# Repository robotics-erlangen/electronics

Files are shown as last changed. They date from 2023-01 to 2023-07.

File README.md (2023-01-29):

# Robotics Erlangen e.V. &ndash; Open Source SSL Robot Hardware
Raw and compiled files for the open source hardware of the German SSL team ER-Force.

## Commit Structure
Commits that have been tagged represent a self-contained robot state,
i.e. the PCB's and mechanical components work well with each other.

## Folder Structure
At the top level of the repository, there is a separate folder for each robot generation.
Currently, only parts of our latest robot generation 'pasta' have been published.
Each robot generation is divided into two sections: mechanics and electronics.

The electronics section has the following structure:
- boards: Contains a separate folder for each PCB that is part of the robot
- eagle: Contains generic libraries, design rule files, etc.

Within each PCB's folder, there are multiple subfolders:
- documents: A pdf version of the schematics as well as optional documentation
- eagle: The schematics and layout in the raw EAGLE file format, i.e.
  - the schematics (*.sch)
  - the layout (*.brd)
  - a library with all board-specific, non-generic components (*.lbr)
  - the design rule file used (*.dru)
  - the cam job used to generate the gerber files (*.cam)
- gerber: The compiled layout files, i.e.
  - the Gerber files
  - the Excellon drill files
  - the Pick & Place files for the top and bottom side
  - a bill of materials

## Example
- ```/pasta```: all files related to the 'pasta' generation
- ```/pasta/electronics```: electronic files for the 'pasta' generation
- ```/pasta/electronics/eagle```: generic eagle files usable accross multiple 'pasta' PCBs
- ```/pasta/electronics/boards```: all PCBs used in the 'pasta' generation
- ```/pasta/electronics/boards/kicker```: all data related to the kicker board of the 'pasta' generation
- ```/pasta/electronics/boards/kicker/eagle```: the raw eagle data of the kicker board
- ```/pasta/electronics/boards/kicker/gerber```: the compiled files of the kicker board
- ```/pasta/electronics/boards/kicker/documents```: additional documentation for the kicker board (e.g. schematics as pdf)

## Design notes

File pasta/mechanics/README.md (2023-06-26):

### What is this repository for? ###

* CAD data for the mechanics of Robotics-Erlangen e.V.
* Generation 2023
* Created  in Autodesk Inventor 2023

### How do I get set up? ###

Project file: When starting Inventor, always make sure that 'OpenSource_2023.ipj' is selected as the active project file. The path in which the working directory is located is noted there for Inventor.

### Folder structure ###

In the file 'Robot_2023.iam' is the assembly of the entire robot. Each folder is assigned to a module of the robot. The production drawings of the components of the modules are stored in the respective folders under 'drawings'. Furthermore, there is the folder 'STEP', where a step file of the robot's assembly can be found, and the folder 'Object_Data', where an object file of the robot is stored. Content centre files are stored in the folder 'ContenCenter-Files'. This concerns all standard parts that are installed via the Content Centre. Other imported parts are stored in the respective subfolders for the corresponding assemblies. The file 'purchased_parts.xlsx' contains a list of our purchased parts.

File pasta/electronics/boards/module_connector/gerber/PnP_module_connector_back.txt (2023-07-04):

C101	-24.50	31.50	90.00	100n ±10% 50V X7R	C0603
C102	-24.50	0.50	90.00	100n ±10% 50V X7R	C0603
C103	24.50	30.50	270.00	100n ±10% 50V X7R	C0603
C104	-24.50	-30.50	90.00	100n ±10% 50V X7R	C0603
C105	24.50	-31.50	270.00	100n ±10% 50V X7R	C0603
C106	24.50	-0.50	270.00	100n ±10% 50V X7R	C0603
C107	5.00	-10.00	90.00	100n ±10% 50V X7R	C0603
J101	0.00	10.00	180.00		610016243021
J102	-35.00	31.00	90.00		610016243021
J103	-35.00	0.00	90.00		610016243021
J104	-35.00	-31.00	90.00		610016243021
J105	35.00	-31.00	270.00		610016243021
J106	35.00	0.00	270.00		610016243021
J107	35.00	31.00	270.00		610016243021
J201	60.00	42.73	270.00		610004243021
J202	60.00	19.27	90.00		610004243021
J203	60.00	11.73	270.00		610004243021
J204	60.00	-11.73	90.00		610004243021
J205	60.00	-19.27	270.00		610004243021
J206	60.00	-42.73	90.00		610004243021
J207	-60.00	-42.73	90.00		610004243021
J208	-60.00	-19.27	270.00		610004243021
J209	-60.00	-11.73	90.00		610004243021
J210	-60.00	11.73	270.00		610004243021
J211	-60.00	19.27	90.00		610004243021
J212	-60.00	42.73	270.00		610004243021
J213	-11.73	35.00	180.00		610004243021
J214	11.73	35.00	0.00		610004243021
R101	1.50	-13.00	180.00	3k3 ±1% 75V 0.1W	R0603
R102	-28.00	28.50	180.00	3k3 ±1% 75V 0.1W	R0603
R103	-28.00	-2.50	180.00	3k3 ±1% 75V 0.1W	R0603
R104	-28.00	-33.50	180.00	3k3 ±1% 75V 0.1W	R0603
R105	28.00	-28.50	0.00	3k3 ±1% 75V 0.1W	R0603
R106	28.00	2.50	0.00	3k3 ±1% 75V 0.1W	R0603
R107	28.00	33.50	0.00	3k3 ±1% 75V 0.1W	R0603
SHORT101	-12.00	1.25	180.00	SHORT0.254	SHORT0.254
SHORT102	-5.00	48.00	0.00	SHORT0.254	SHORT0.254
SHORT105	0.00	-47.00	180.00	SHORT0.254	SHORT0.254
SHORT108	15.00	48.00	0.00	SHORT0.254	SHORT0.254
U101	1.50	-10.00	180.00	SN74AUP1G126DBVR	SOT23-5
U102	-28.00	31.50	180.00	SN74AUP1G126DBVR	SOT23-5
U103	-28.00	0.50	180.00	SN74AUP1G126DBVR	SOT23-5
U104	-28.00	-30.50	180.00	SN74AUP1G126DBVR	SOT23-5
U105	28.00	-31.50	0.00	SN74AUP1G126DBVR	SOT23-5
U106	28.00	-0.50	0.00	SN74AUP1G126DBVR	SOT23-5
U107	28.00	30.50	0.00	SN74AUP1G126DBVR	SOT23-5

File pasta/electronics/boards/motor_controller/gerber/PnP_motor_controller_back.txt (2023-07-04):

C101	14.50	16.00	0.00	100n ±10% 50V X5R	C0402
C102	9.50	33.50	180.00	1u ±10% 25V X5R	C0402
C103	3.50	4.00	180.00	4u7 ±20% 6V3 X5R	C0603
C104	3.50	6.00	180.00	4u7 ±20% 6V3 X5R	C0603
C201	15.00	12.00	180.00	100n ±10% 50V X5R	C0402
C203	8.00	12.50	270.00	4u7 ±20% 6V3 X5R	C0603
C204	6.00	13.50	270.00	100n ±10% 50V X5R	C0402
C205	10.50	12.00	90.00	100n ±10% 50V X5R	C0402
C206	9.50	15.50	270.00	100n ±10% 50V X5R	C0402
C207	10.50	15.50	270.00	1u ±10% 25V X5R	C0402
C208	11.50	13.00	270.00	100n ±10% 50V X5R	C0402
D401	-8.50	23.00	270.00	D15V0M1U2LP3	D15V0M1U2LP3
D402	-10.50	23.00	270.00	D15V0M1U2LP3	D15V0M1U2LP3
D403	-2.50	21.00	0.00	D15V0M1U2LP3	D15V0M1U2LP3
D404	0.50	21.00	0.00	D15V0M1U2LP3	D15V0M1U2LP3
D405	11.50	22.50	270.00	D15V0M1U2LP3	D15V0M1U2LP3
D406	9.50	24.00	180.00	D15V0M1U2LP3	D15V0M1U2LP3
L101	0.50	5.00	90.00	742792692	WE-CBF_0603(W=2.6)
R102	14.50	18.00	0.00	1k ±1% 50V 62.5mW	R0402
R201	6.00	7.50	0.00	1k ±1% 50V 62.5mW	R0402
R203	-3.00	34.50	270.00	1k ±1% 50V 62.5mW	R0402
R204	-5.00	34.50	270.00	1k ±1% 50V 62.5mW	R0402
R205	3.00	34.50	270.00	1k ±1% 50V 62.5mW	R0402
R302	5.50	10.00	270.00	1k ±1% 50V 62.5mW	R0402
R403	-12.50	23.00	270.00	0R ±1% 50V 62.5mW	R0402
R404	0.50	23.00	0.00	0R ±1% 50V 62.5mW	R0402
R407	-7.50	24.00	90.00	0R ±1% 50V 62.5mW	R0402
R408	-2.50	23.00	0.00	0R ±1% 50V 62.5mW	R0402
R409	-9.50	23.00	90.00	n.c.   	R0402
R410	-11.50	23.00	90.00	n.c.   	R0402
R411	-2.50	22.00	180.00	n.c.   	R0402
R412	0.50	22.00	180.00	n.c.   	R0402
R414	8.00	25.50	270.00	0R ±1% 50V 62.5mW	R0402
R416	9.50	22.50	270.00	0R ±1% 50V 62.5mW	R0402
R417	10.50	22.50	90.00	n.c.   	R0402
R418	9.50	25.00	0.00	n.c.   	R0402
Z103	-5.00	25.50	180.00	ESD8704	UDFN10
Z104	-2.00	25.50	180.00	ESD8704	UDFN10
Z105	5.00	25.50	180.00	ESD7004	UDFN10

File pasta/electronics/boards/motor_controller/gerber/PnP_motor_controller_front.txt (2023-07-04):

C105	-5.00	4.50	270.00	100n ±10% 50V X5R	C0402
C106	-4.00	4.50	270.00	1u ±10% 25V X5R	C0402
C107	-1.50	4.50	270.00	100n ±10% 50V X5R	C0402
C108	-0.50	4.50	270.00	1u ±10% 25V X5R	C0402
C202	12.50	8.50	270.00	100n ±10% 50V X5R	C0402
C301	-6.80	7.00	180.00	100n ±10% 50V X5R	C0402
C302	-12.50	15.50	270.00	100u ±20% 35V	865080545012
C303	-6.00	14.00	90.00	10u ±20% 50V X5R	C1206
C304	-3.50	14.50	90.00	100n ±10% 50V X7R	C0603
C305	-3.50	12.00	0.00	1u ±10% 25V X5R	C0402
C306	-0.25	16.00	90.00	1u ±10% 25V X5R	C0402
C307	-2.00	16.00	90.00	47n ±10% 50V X5R	C0402
C308	0.75	16.00	90.00	1u ±10% 25V X5R	C0402
C401	-13.00	24.50	90.00	n.c.   	C0402
C402	3.00	23.50	90.00	n.c.   	C0402
C403	-10.00	20.50	0.00	1u ±10% 50V X5R	C0603
C404	-1.00	19.50	180.00	1u ±10% 50V X5R	C0603
C405	-6.50	24.50	270.00	n.c.   	C0402
C406	-4.50	23.50	270.00	n.c.   	C0402
C407	7.00	23.50	90.00	n.c.   	C0402
C408	10.00	19.50	0.00	1u ±10% 50V X5R	C0603
C409	13.00	23.50	270.00	n.c.   	C0402
D201	0.00	35.00	180.00	150066M153000	WL-SFCX_0606
F101	-13.00	5.00	180.00	5A	157T
L102	-1.50	6.50	0.00	782632102	WE-CBF_0603(W=2.6)
R101	-5.00	6.50	90.00	2R2 ±1% 50V 62.5mW	R0402
R202	9.50	8.50	90.00	1k ±1% 50V 62.5mW	R0402
R301	-14.34	9.50	270.00	FC4L32R010FER	FC4L32
R401	-12.00	26.50	180.00	n.c.   	R0603
R402	2.00	25.50	0.00	n.c.   	R0603
R405	-8.00	26.50	180.00	n.c.   	R0603
R406	-2.00	25.50	0.00	n.c.   	R0603
R413	8.00	25.50	180.00	n.c.   	R0603
R415	12.00	25.50	180.00	n.c.   	R0603
SHORT101	-7.50	15.50	0.00	SHORT4.35	SHORT4.35
SHORT102	-5.95	6.00	180.00	SHORT2.4	SHORT2.4
SHORT103	-5.95	4.00	180.00	SHORT2.4	SHORT2.4
SHORT301	-4.50	12.00	0.00	SHORT2.4	SHORT2.4
T401	-10.00	23.50	0.00	SIZ260DT	SIZ260DT
T402	0.00	22.50	180.00	SIZ260DT	SIZ260DT
T403	10.00	22.50	0.00	SIZ260DT	SIZ260DT
U101	14.50	17.00	270.00	SN74AHC1G125DBVR	SOT23-5
U201	8.50	13.50	180.00	STM32F373V8H6	STM32F373V8H6
U202	11.00	8.50	270.00	24CW1280T-I/CS0668	CS0-4
U301	-9.00	9.50	0.00	INA240A3PWR	TSSOP-8
U302	1.00	12.00	0.00	DRV8350FSRTVR	QFN50P500X500X80-33T345
Y201	14.50	12.00	90.00	8 MHz	830207192009
Z101	5.50	5.00	0.00	ESD8704	UDFN10
Z102	8.50	5.00	0.00	ESD8704	UDFN10

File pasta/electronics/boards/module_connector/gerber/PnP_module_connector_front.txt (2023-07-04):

C108	14.00	-48.00	270.00	10u ±20% 50V X5R	C1206
C109	23.50	-6.50	270.00	10u ±20% 50V X5R	C1206
C110	-23.50	5.50	270.00	10u ±20% 50V X5R	C1206
J108	1.27	-73.00	270.00		610004243021
J109	0.00	-50.00	180.00	610016243021	610X16243021
SHORT103	-45.00	15.50	270.00	SHORT0.254	SHORT0.254
SHORT104	-45.00	-15.50	270.00	SHORT0.254	SHORT0.254
SHORT106	45.00	-15.50	90.00	SHORT0.254	SHORT0.254
SHORT107	45.00	15.50	90.00	SHORT0.254	SHORT0.254
TP201	80.00	24.00	270.00	TESTPAD	TESTPAD
TP202	80.00	20.00	270.00	TESTPAD	TESTPAD
TP203	80.00	12.00	270.00	TESTPAD	TESTPAD
TP204	80.00	16.00	270.00	TESTPAD	TESTPAD
TP205	80.00	6.00	0.00	TESTPAD	TESTPAD
TP206	80.00	2.00	0.00	TESTPAD	TESTPAD
TP207	80.00	-2.00	0.00	TESTPAD	TESTPAD
TP208	80.00	-6.00	0.00	TESTPAD	TESTPAD
TP209	80.00	-16.00	0.00	TESTPAD	TESTPAD
TP210	80.00	-12.00	0.00	TESTPAD	TESTPAD
TP211	80.00	-20.00	0.00	TESTPAD	TESTPAD
TP212	80.00	-24.00	0.00	TESTPAD	TESTPAD
TP213	-80.00	-24.00	0.00	TESTPAD	TESTPAD
TP214	-80.00	-20.00	0.00	TESTPAD	TESTPAD
TP215	-80.00	-12.00	0.00	TESTPAD	TESTPAD
TP216	-80.00	-16.00	0.00	TESTPAD	TESTPAD
TP217	-80.00	-6.00	0.00	TESTPAD	TESTPAD
TP218	-80.00	-2.00	0.00	TESTPAD	TESTPAD
TP219	-80.00	2.00	0.00	TESTPAD	TESTPAD
TP220	-80.00	6.00	0.00	TESTPAD	TESTPAD
TP221	-80.00	16.00	0.00	TESTPAD	TESTPAD
TP222	-80.00	12.00	0.00	TESTPAD	TESTPAD
TP223	-80.00	20.00	0.00	TESTPAD	TESTPAD
TP224	-80.00	24.00	0.00	TESTPAD	TESTPAD
TP225	-23.50	43.00	0.00	TESTPAD	TESTPAD
TP226	-23.50	47.00	180.00	TESTPAD	TESTPAD
TP227	23.50	47.00	0.00	TESTPAD	TESTPAD
TP228	23.50	43.00	180.00	TESTPAD	TESTPAD

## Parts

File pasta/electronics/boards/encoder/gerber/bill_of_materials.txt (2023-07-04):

Stückliste exportiert aus D:/hardware/pasta/electronics/boards/encoder/eagle/encoder.sch am 04.07.2023 16:03

Part Value        Device                Package      Description                                                                                      CAPACITANCE COPYRIGHT                                                DIELECTRIC MF                        MOUSER               MPN               POWER RESISTANCE TOLERANCE VOLTAGE
C101 4u7 6V3      C(4.7UF,50V,0805)     C0805        Robotics Erlangen Capacitor Library                                                              4u7                                                                  X5R        Samsung                                        CL21A475KBQNNNE                    ±10%      50V    
C102 100n 6V3     C(100NF,50V,0603)     C0603        Robotics Erlangen Capacitor Library                                                              100n                                                                 X7R        Würth Elektronik                               885012206095                       ±10%      50V    
C103 10u 6V3      C(10UF,6.3V,0603)     C0603        Robotics Erlangen Capacitor Library                                                              10u                                                                  X5R        Würth Elektronik                               885012106006                       ±20%      6V3    
C104 10n 50V      C(10NF,50V,0603)      C0603        Robotics Erlangen Capacitor Library                                                              10n                                                                  X7R        Würth Elektronik                               885012206089                       ±10%      50V    
C105 100n 6V3     C(100NF,50V,0603)     C0603        Robotics Erlangen Capacitor Library                                                              100n                                                                 X7R        Würth Elektronik                               885012206095                       ±10%      50V    
D101 PTVS3V3S1UR  PTVS3V3S1UR           SOD123                                                                                                                                                                                        Nexperia                  771-PTVS3V3S1UR115    PTVS3V3S1UR,115                                    
J101 690367281076 690367281076          690367281076 WR-MM Female SMT Connector with Polarization, 10 Pins=>Code : Con_BTB_MM_Female_SMT_690367281076                                                                                 Würth Elektronik                               690367281076                                        
R101 10k          R(10K,75V,0.1W,0603)  R0603        Robotics Erlangen Resistor Library                                                                                                                                               YAGEO                                          RC0603FR-0710KL   0.1W  10k        ±1%       75V    
R102 10k          R(10K,75V,0.1W,0603)  R0603        Robotics Erlangen Resistor Library                                                                                                                                               YAGEO                                          RC0603FR-0710KL   0.1W  10k        ±1%       75V    
R103 100R         R(100R,75V,0.1W,0603) R0603        Robotics Erlangen Resistor Library                                                                                                                                               YAGEO                                          RC0603FR-07100RL  0.1W  100R       ±1%       75V    
R104 100R         R(100R,75V,0.1W,0603) R0603        Robotics Erlangen Resistor Library                                                                                                                                               YAGEO                                          RC0603FR-07100RL  0.1W  100R       ±1%       75V    
R105 100R         R(100R,75V,0.1W,0603) R0603        Robotics Erlangen Resistor Library                                                                                                                                               YAGEO                                          RC0603FR-07100RL  0.1W  100R       ±1%       75V    
R106 100R         R(100R,75V,0.1W,0603) R0603        Robotics Erlangen Resistor Library                                                                                                                                               YAGEO                                          RC0603FR-07100RL  0.1W  100R       ±1%       75V    
R107 1k           R(1.0K,75V,0.1W,0603) R0603        Robotics Erlangen Resistor Library                                                                                                                                               YAGEO                                          RC0603FR-071KL    0.1W  1k         ±1%       75V    
R108 1k           R(1.0K,75V,0.1W,0603) R0603        Robotics Erlangen Resistor Library                                                                                                                                               YAGEO                                          RC0603FR-071KL    0.1W  1k         ±1%       75V    
T101 BSS123       BSS123                SOT23-3      N-CHANNEL MOS FET                                                                                                                                                                Nexperia                  726-BSS123NH6327XTSA BSS123NH6327XTSA1                                   
U101 AS5048A-HTSP AS5048A-HTSP          AS5048A-HTSP                                                                                                                                                                                  ams                       985-AS5048A-HTSP-500 AS5048A-HTSP                                        
U102 MAX9130EXT+T MAX9130EXT+T          21-0077G_MXM                                                                                                              Copyright (C) 2021 Ultra Librarian. All rights reserved.            Maxim Integrated Products                      MAX9130EXT+T                                        
U103 SN65LVDS050D SN65LVDS050D          SOIC-16                                                                                                                                                                                       Texas Instruments                              SN65LVDS050D

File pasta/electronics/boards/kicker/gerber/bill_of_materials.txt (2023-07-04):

Stückliste exportiert aus D:/hardware/pasta/electronics/boards/kicker/eagle/kicker.sch am 04.07.2023 12:32

Part  Value                  Device                         Package                Description                                                                                                          CAPACITANCE DIELECTRIC LINE1     LINE2      MF                           MOUSER               MPN                 POWER RESISTANCE TOLERANCE VALUE               VOLTAGE
C101  270  µF                WCAP-PSLC_10X12.4_875075661009 WCAP-PSLC_10X12.4(DXL) WCAP-PSLC Aluminum Polymer Capacitors                                                                                                                            Würth Elektronik                                  875075661009                         ±10%      270  µF             35V(DC)
C102  10u ±20% 50V X5R       C(10UF,50V,1206)               C1206                  Robotics Erlangen Capacitor Library                                                                                  10u         X5R        10u ±20%  50V X5R    Samsung                                           CL31A106MBHNNNE                      ±20%      10u ±20% 50V X5R    50V    
C103  100n ±10% 50V X7R      C(100NF,50V,0603)              C0603                  Robotics Erlangen Capacitor Library                                                                                  100n        X7R        100n ±10% 50V X7R    Würth Elektronik                                  885012206095                         ±10%      100n ±10% 50V X7R   50V    
C104  100n ±10% 50V X7R      C(100NF,50V,0603)              C0603                  Robotics Erlangen Capacitor Library                                                                                  100n        X7R        100n ±10% 50V X7R    Würth Elektronik                                  885012206095                         ±10%      100n ±10% 50V X7R   50V    
C105  4u7 ±10% 50V X5R       C(4.7UF,50V,0805)              C0805                  Robotics Erlangen Capacitor Library                                                                                  4u7         X5R        4u7 ±10%  50V X5R    Samsung                                           CL21A475KBQNNNE                      ±10%      4u7 ±10% 50V X5R    50V    
C106  100p ±5% 50V NP0       C(100PF,50V,0603)              C0603                  Robotics Erlangen Capacitor Library                                                                                  100p        NP0        100p ±5%  50V NP0    Würth Elektronik                                  885012006057                         ±5%       100p ±5% 50V NP0    50V    
C107  2n2 ±10% 50V X7R       C(2.2NF,50V,0603)              C0603                  Robotics Erlangen Capacitor Library                                                                                  2n2         X7R        2n2 ±10%  50V X7R    Würth Elektronik                                  885012206085                         ±10%      2n2 ±10% 50V X7R    50V    
C108  33n ±10% 50V X7R       C(33NF,50V,0603)               C0603                  Robotics Erlangen Capacitor Library                                                                                  33n         X7R        33n ±10%  50V X7R    Würth Elektronik                                  885012206092                         ±10%      33n ±10% 50V X7R    50V    
C109                         C(1210)                        C1210                  Robotics Erlangen Capacitor Library                                                                                  220nF       X7R        220n ±5%  100V X7R   KEMET                                             C0805C224J1RECTU                     ±5%                           100V   
C110  n.c.                   C(N.C.,1206)                   C1206                  Robotics Erlangen Capacitor Library                                                                                  n.c.                   n.c.                                                                                                                  n.c.                       
C111  n.c.                   C(N.C.,1206)                   C1206                  Robotics Erlangen Capacitor Library                                                                                  n.c.                   n.c.                                                                                                                  n.c.                       
C112  1000u 250V             ESMQ251VSN102MQ45S             ESMQ251VSN102MQ45S                                                                                                                                                                      United Chemi-Con             661-ESMQ251VSN102MQ4 ESMQ251VSN102MQ45S                                                        
C113  1000u 250V             ESMQ251VSN102MQ45S             ESMQ251VSN102MQ45S                                                                                                                                                                      United Chemi-Con             661-ESMQ251VSN102MQ4 ESMQ251VSN102MQ45S                                                        
C201  47n ±10% 50V X7R       C(47NF,50V,0603)               C0603                  Robotics Erlangen Capacitor Library                                                                                  47n         X7R        47n ±10%  50V X7R    Würth Elektronik                                  885012206093                         ±10%      47n ±10% 50V X7R    50V    
C202  47n ±10% 50V X7R       C(47NF,50V,0603)               C0603                  Robotics Erlangen Capacitor Library                                                                                  47n         X7R        47n ±10%  50V X7R    Würth Elektronik                                  885012206093                         ±10%      47n ±10% 50V X7R    50V    
C203  1u ±10% 50V X5R        C(1.0UF,50V,0603)              C0603                  Robotics Erlangen Capacitor Library                                                                                  1u          X5R        1u ±10%   50V X5R    Samsung                                           CL10A105KB8NNNC                      ±10%      1u ±10% 50V X5R     50V    
C204  1u ±10% 50V X5R        C(1.0UF,50V,0603)              C0603                  Robotics Erlangen Capacitor Library                                                                                  1u          X5R        1u ±10%   50V X5R    Samsung                                           CL10A105KB8NNNC                      ±10%      1u ±10% 50V X5R     50V    
C205  10u ±20% 50V X5R       C(10UF,50V,1206)               C1206                  Robotics Erlangen Capacitor Library                                                                                  10u         X5R        10u ±20%  50V X5R    Samsung                                           CL31A106MBHNNNE                      ±20%      10u ±20% 50V X5R    50V    
C206                         C(1210)                        C1210                  Robotics Erlangen Capacitor Library                                                                                  330n        X7T        330n ±10% X7T 250V   TDK                                               C3225X7T2E334K200AA                  ±10%                          250V   
C207  10u ±20% 50V X5R       C(10UF,50V,1206)               C1206                  Robotics Erlangen Capacitor Library                                                                                  10u         X5R        10u ±20%  50V X5R    Samsung                                           CL31A106MBHNNNE                      ±20%      10u ±20% 50V X5R    50V    
C208  10u ±20% 50V X5R       C(10UF,50V,1206)               C1206                  Robotics Erlangen Capacitor Library                                                                                  10u         X5R        10u ±20%  50V X5R    Samsung                                           CL31A106MBHNNNE                      ±20%      10u ±20% 50V X5R    50V    
C301  100n ±10% 50V X7R      C(100NF,50V,0603)              C0603                  Robotics Erlangen Capacitor Library                                                                                  100n        X7R        100n ±10% 50V X7R    Würth Elektronik                                  885012206095                         ±10%      100n ±10% 50V X7R   50V    
C302  100n ±10% 50V X7R      C(100NF,50V,0603)              C0603                  Robotics Erlangen Capacitor Library                                                                                  100n        X7R        100n ±10% 50V X7R    Würth Elektronik                                  885012206095                         ±10%      100n ±10% 50V X7R   50V    
C303  100n ±10% 50V X7R      C(100NF,50V,0603)              C0603                  Robotics Erlangen Capacitor Library                                                                                  100n        X7R        100n ±10% 50V X7R    Würth Elektronik                                  885012206095                         ±10%      100n ±10% 50V X7R   50V    
C304  2u2 ±10% 50V X7R       C(2.2UF,50V,0805)              C0805                  Robotics Erlangen Capacitor Library                                                                                  2u2         X7R        2u2 ±10%  50V X7R    Samsung                                           CL21B225KBYNNWE                      ±10%      2u2 ±10% 50V X7R    50V    
C305  100n ±10% 50V X7R      C(100NF,50V,0603)              C0603                  Robotics Erlangen Capacitor Library                                                                                  100n        X7R        100n ±10% 50V X7R    Würth Elektronik                                  885012206095                         ±10%      100n ±10% 50V X7R   50V    
D101                         LED5MM                         LED5MM                                                                                                                                                                                  Würth Elektronik                                  151054RS03000                                                             
D102  1N4148                 1N4148W                        SOD-123                DIODE                                                                                                                                                            Micro Commercial Components                       1N4148W                                                                   
D103  STTH212U               STTH212U                       SMB                    DIODE                                                                                                                                                            STMicroelectronics                                STTH212U                                                                  
D201  GB01SLT12-214          GB01SLT12-214                  DO-214                                                                                                                                                                                  GeneSiC                      905-GB01SLT06-214    GB01SLT06-214                                                             
D202  GB01SLT12-214          GB01SLT12-214                  DO-214                                                                                                                                                                                  GeneSiC                      905-GB01SLT06-214    GB01SLT06-214                                                             
D203  GB01SLT12-214          GB01SLT12-214                  DO-214                                                                                                                                                                                  GeneSiC                      905-GB01SLT06-214    GB01SLT06-214                                                             
D204  GB01SLT12-214          GB01SLT12-214                  DO-214                                                                                                                                                                                  GeneSiC                      905-GB01SLT06-214    GB01SLT06-214                                                             
H101                         9774060360R                    9774***360                                                                                                                                                                              Würth Elektronik                                  9774060360R                                                               
H102                         9774060360R                    9774***360                                                                                                                                                                              Würth Elektronik                                  9774060360R                                                               
H103                         9774060360R                    9774***360                                                                                                                                                                              Würth Elektronik                                  9774060360R                                                               
J301                         690367181672                   690367181672           WR-MM Female Connector without Latch and without Polarization, 16 Pins=>Code : Con_BTB_MM_Female_THT_St_690367181672                                             Würth Elektronik                                  690367181672                                                              
J302                         66100311622                    66100311622*           Male Vertical Shrouded Header                                                                                                                                    Würth Elektronik                                  66100311622                                                               
J303                         66100311622                    66100311622*           Male Vertical Shrouded Header                                                                                                                                    Würth Elektronik                                  66100311622                                                               
OP101 LTV-352T               LTV-352T                       DIL4-SMD               OPTO COUPLER                                                                                                                                                     Lite-On                      859-LTV-352T         LTV-352T                                                                  
OP201 LTV-352T               LTV-352T                       DIL4-SMD               OPTO COUPLER                                                                                                                                                     Lite-On                      859-LTV-352T         LTV-352T                                                                  
OP202 LTV-352T               LTV-352T                       DIL4-SMD               OPTO COUPLER                                                                                                                                                     Lite-On                      859-LTV-352T         LTV-352T                                                                  
Q101  FJT44TF                TRANSISTOR_NPN"                SOT223                 Transistor NPN                                                                                                                                                   onsemi / Fairchild                                FJT44TF                                                                   
Q102  TPH3300CNH             TPH3300CNH                     SOP-8                                                                                                                                                                                   Toshiba                      757-TPH3300CNHL1Q    TPH3300CNH                                                                
Q201  IXYT55N120A4HV         IXYT55N120A4HV                 TO-268HV                                                                                                                                                                                IXYS                         747-IXYT55N120A4HV   IXYT55N120A4HV                                                            
Q202  IXYT55N120A4HV         IXYT55N120A4HV                 TO-268HV                                                                                                                                                                                IXYS                         747-IXYT55N120A4HV   IXYT55N120A4HV                                                            
R101  270R ±1% 75V 0.1W      R(270R,75V,0.1W,0603)          R0603                  Robotics Erlangen Resistor Library                                                                                                          270R ±1%  75V 0.1W   YAGEO                                             RC0603FR-07270RL    0.1W  270R       ±1%       270R ±1% 75V 0.1W   75V    
R102                         R(2512)                        R2512                  Robotics Erlangen Resistor Library                                                                                                          330k ±1%  500V 2W    TE Connectivity / Holsworthy                      CRGP2512F330K       2W    330k       ±1%                           500V   
R103                         R(2512)                        R2512                  Robotics Erlangen Resistor Library                                                                                                          33k ±1%   500V 2W    TE Connectivity / Holsworthy                      CRGP2512F33K        2W    33k        1%                            500V   
R104                         R(2512)                        R2512                  Robotics Erlangen Resistor Library                                                                                                          470k ±5%  500V 1.5W  Vishay / Dale                                     CRCW2512470KJNEGHP  1.5W  470k       ±5%                           500V   
R105                         R(0603)                        R0603                  Robotics Erlangen Resistor Library                                                                                                          24k9 ±1%  75V 100mW  YAGEO                                             RE0603FRE0724K9L    100mW 24k9       ±1%                           75V    
R106  4R7 ±1% 75V 0.1W       R(4.7R,75V,0.1W,0603)          R0603                  Robotics Erlangen Resistor Library                                                                                                          4R7 ±1%   75V 0.1W   YAGEO                                             RC0603FR-074R7L     0.1W  4R7        ±1%       4R7 ±1% 75V 0.1W    75V    
R107                         R(0603)                        R0603                  Robotics Erlangen Resistor Library                                                                                                          249k ±1%  75V 100mW  YAGEO                                             RC0603FR-07249KL    100mW 249k       ±1%                           75V    
R108                         R(0603)                        R0603                  Robotics Erlangen Resistor Library                                                                                                          51k1 ±1%  75V 100mW  YAGEO                                             RC0603FR-0751K1L    100mW 51k1       ±1%                           75V    
R109                         R(0603)                        R0603                  Robotics Erlangen Resistor Library                                                                                                          6k04 ±1%  75V 100mW  YAGEO                                             AC0603FR-136K04L    100mW 6k04       ±1%                           75V    
R110                         R(1206)                        R1206                  Robotics Erlangen Resistor Library                                                                                                          15m ±1%   1W         Panasonic                                         ERJ-8BWFR015V       1W    15m        ±1%                                  
R111  100k ±1% 200V 0.25W    R(100K,200V,0.25W,1206)        R1206                  Robotics Erlangen Resistor Library                                                                                                          100k ±1%  200V 0.25W YAGEO                                             RC1206FR-07100KL    0.25W 100k       ±1%       100k ±1% 200V 0.25W 200V   
R112  n.c.                   R(N.C.,1206)                   R1206                  Robotics Erlangen Resistor Library                                                                                                          n.c.                                                                                             n.c.                 n.c.                       
R201  22R ±1% 75V 0.1W       R(22R,75V,0.1W,0603)           R0603                  Robotics Erlangen Resistor Library                                                                                                          22R ±1%   75V 0.1W   YAGEO                                             RC0603FR-0722RL     0.1W  22R        ±1%       22R ±1% 75V 0.1W    75V    
R202  22R ±1% 75V 0.1W       R(22R,75V,0.1W,0603)           R0603                  Robotics Erlangen Resistor Library                                                                                                          22R ±1%   75V 0.1W   YAGEO                                             RC0603FR-0722RL     0.1W  22R        ±1%       22R ±1% 75V 0.1W    75V    
R203  1k ±1% 75V 0.1W        R(1.0K,75V,0.1W,0603)          R0603                  Robotics Erlangen Resistor Library                                                                                                          1k ±1%    75V 0.1W   YAGEO                                             RC0603FR-071KL      0.1W  1k         ±1%       1k ±1% 75V 0.1W     75V    
R204  1k ±1% 75V 0.1W        R(1.0K,75V,0.1W,0603)          R0603                  Robotics Erlangen Resistor Library                                                                                                          1k ±1%    75V 0.1W   YAGEO                                             RC0603FR-071KL      0.1W  1k         ±1%       1k ±1% 75V 0.1W     75V    
R205  1k5 ±1% 75V 0.1W       R(1.5K,75V,0.1W,0603)          R0603                  Robotics Erlangen Resistor Library                                                                                                          1k5 ±1%   75V 0.1W   YAGEO                                             RC0603FR-071K5L     0.1W  1k5        ±1%       1k5 ±1% 75V 0.1W    75V    
R206  1k5 ±1% 75V 0.1W       R(1.5K,75V,0.1W,0603)          R0603                  Robotics Erlangen Resistor Library                                                                                                          1k5 ±1%   75V 0.1W   YAGEO                                             RC0603FR-071K5L     0.1W  1k5        ±1%       1k5 ±1% 75V 0.1W    75V    
R207  0R ±1% 75V 0.1W        R(0R,75V,0.1W,0603)            R0603                  Robotics Erlangen Resistor Library                                                                                                          0R ±1%    75V 0.1W   YAGEO                                             RC0603FR-070RL      0.1W  0R         ±1%       0R ±1% 75V 0.1W     75V    
R208  3R3 ±1% 75V 0.1W       R(3.3R,75V,0.1W,0603)          R0603                  Robotics Erlangen Resistor Library                                                                                                          3R3 ±1%   75V 0.1W   YAGEO                                             RC0603FR-073R3L     0.1W  3R3        ±1%       3R3 ±1% 75V 0.1W    75V    
R209  0R ±1% 75V 0.1W        R(0R,75V,0.1W,0603)            R0603                  Robotics Erlangen Resistor Library                                                                                                          0R ±1%    75V 0.1W   YAGEO                                             RC0603FR-070RL      0.1W  0R         ±1%       0R ±1% 75V 0.1W     75V    
R210  3R3 ±1% 75V 0.1W       R(3.3R,75V,0.1W,0603)          R0603                  Robotics Erlangen Resistor Library                                                                                                          3R3 ±1%   75V 0.1W   YAGEO                                             RC0603FR-073R3L     0.1W  3R3        ±1%       3R3 ±1% 75V 0.1W    75V    
R211  3R3                    R-EU_3R3-R4527                 R4527                                                                                                                                                                                   TE Connectivity / Holsworthy                      35603R3JT                                                                 
R212  3R3                    R-EU_3R3-R4527                 R4527                                                                                                                                                                                   TE Connectivity / Holsworthy                      35603R3JT                                                                 
R213  0R ±1% 75V 0.1W        R(0R,75V,0.1W,0603)            R0603                  Robotics Erlangen Resistor Library                                                                                                          0R ±1%    75V 0.1W   YAGEO                                             RC0603FR-070RL      0.1W  0R         ±1%       0R ±1% 75V 0.1W     75V    
R214  0R ±1% 75V 0.1W        R(0R,75V,0.1W,0603)            R0603                  Robotics Erlangen Resistor Library                                                                                                          0R ±1%    75V 0.1W   YAGEO                                             RC0603FR-070RL      0.1W  0R         ±1%       0R ±1% 75V 0.1W     75V    
R301  150R ±1% 75V 0.1W      R(150R,75V,0.1W,0603)          R0603                  Robotics Erlangen Resistor Library                                                                                                          150R ±1%  75V 0.1W   YAGEO                                             RC0603FR-07150RL    0.1W  150R       ±1%       150R ±1% 75V 0.1W   75V    
R302                         R(2010)                        R2010                  Robotics Erlangen Resistor Library                                                                                                          1M ±5%    200V 0.75W YAGEO                                             RC2010JK-071ML      0.75W 1M         ±5%                           200V   
R303  150R ±1% 75V 0.1W      R(150R,75V,0.1W,0603)          R0603                  Robotics Erlangen Resistor Library                                                                                                          150R ±1%  75V 0.1W   YAGEO                                             RC0603FR-07150RL    0.1W  150R       ±1%       150R ±1% 75V 0.1W   75V    
R304  10k ±1% 75V 0.1W       R(10K,75V,0.1W,0603)           R0603                  Robotics Erlangen Resistor Library                                                                                                          10k ±1%   75V 0.1W   YAGEO                                             RC0603FR-0710KL     0.1W  10k        ±1%       10k ±1% 75V 0.1W    75V    
R305  100R ±1% 75V 0.1W      R(100R,75V,0.1W,0603)          R0603                  Robotics Erlangen Resistor Library                                                                                                          100R ±1%  75V 0.1W   YAGEO                                             RC0603FR-07100RL    0.1W  100R       ±1%       100R ±1% 75V 0.1W   75V    
R306  100R ±1% 75V 0.1W      R(100R,75V,0.1W,0603)          R0603                  Robotics Erlangen Resistor Library                                                                                                          100R ±1%  75V 0.1W   YAGEO                                             RC0603FR-07100RL    0.1W  100R       ±1%       100R ±1% 75V 0.1W   75V    
R307  100R ±1% 75V 0.1W      R(100R,75V,0.1W,0603)          R0603                  Robotics Erlangen Resistor Library                                                                                                          100R ±1%  75V 0.1W   YAGEO                                             RC0603FR-07100RL    0.1W  100R       ±1%       100R ±1% 75V 0.1W   75V    
R308  100R ±1% 75V 0.1W      R(100R,75V,0.1W,0603)          R0603                  Robotics Erlangen Resistor Library                                                                                                          100R ±1%  75V 0.1W   YAGEO                                             RC0603FR-07100RL    0.1W  100R       ±1%       100R ±1% 75V 0.1W   75V
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

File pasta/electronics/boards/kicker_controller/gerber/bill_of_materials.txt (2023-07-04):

Stückliste exportiert aus D:/hardware/pasta/electronics/boards/kicker_controller/eagle/kicker_controller.sch am 04.07.2023 12:30

Part Value             Device                 Package            Description                                              CAPACITANCE DIELECTRIC LINE1     LINE2    MF                 MOUSER               MOUSER-NR      MPN              POPULARITY POWER RESISTANCE TOLERANCE VALUE             VOLTAGE WE-NUMBER       
C101 100n ±10% 50V X7R C(100NF,50V,0603)      C0603              Robotics Erlangen Capacitor Library                      100n        X7R        100n ±10% 50V X7R  Würth Elektronik                                       885012206095                                 ±10%      100n ±10% 50V X7R 50V                     
C102 100n ±10% 50V X7R C(100NF,50V,0603)      C0603              Robotics Erlangen Capacitor Library                      100n        X7R        100n ±10% 50V X7R  Würth Elektronik                                       885012206095                                 ±10%      100n ±10% 50V X7R 50V                     
C103 100n ±10% 50V X7R C(100NF,50V,0603)      C0603              Robotics Erlangen Capacitor Library                      100n        X7R        100n ±10% 50V X7R  Würth Elektronik                                       885012206095                                 ±10%      100n ±10% 50V X7R 50V                     
C104 100n ±10% 50V X7R C(100NF,50V,0603)      C0603              Robotics Erlangen Capacitor Library                      100n        X7R        100n ±10% 50V X7R  Würth Elektronik                                       885012206095                                 ±10%      100n ±10% 50V X7R 50V                     
C105 100n ±10% 50V X7R C(100NF,50V,0603)      C0603              Robotics Erlangen Capacitor Library                      100n        X7R        100n ±10% 50V X7R  Würth Elektronik                                       885012206095                                 ±10%      100n ±10% 50V X7R 50V                     
C106 100n ±10% 50V X7R C(100NF,50V,0603)      C0603              Robotics Erlangen Capacitor Library                      100n        X7R        100n ±10% 50V X7R  Würth Elektronik                                       885012206095                                 ±10%      100n ±10% 50V X7R 50V                     
C201 100u ±20% 35V     865080545012           865080545012                                                                                                          Würth Elektronik                                       865080545012                                           100u ±20% 35V                             
C202 10u ±20% 6V3 X5R  C(10UF,6.3V,0603)      C0603              Robotics Erlangen Capacitor Library                      10u         X5R        10u ±20%  6V3 X5R  Würth Elektronik                                       885012106006                                 ±20%      10u ±20% 6V3 X5R  6V3                     
C203 100n ±10% 50V X7R C(100NF,50V,0603)      C0603              Robotics Erlangen Capacitor Library                      100n        X7R        100n ±10% 50V X7R  Würth Elektronik                                       885012206095                                 ±10%      100n ±10% 50V X7R 50V                     
C204 100n ±10% 50V X7R C(100NF,50V,0603)      C0603              Robotics Erlangen Capacitor Library                      100n        X7R        100n ±10% 50V X7R  Würth Elektronik                                       885012206095                                 ±10%      100n ±10% 50V X7R 50V                     
C205 100n ±10% 50V X7R C(100NF,50V,0603)      C0603              Robotics Erlangen Capacitor Library                      100n        X7R        100n ±10% 50V X7R  Würth Elektronik                                       885012206095                                 ±10%      100n ±10% 50V X7R 50V                     
C206 100n ±10% 50V X7R C(100NF,50V,0603)      C0603              Robotics Erlangen Capacitor Library                      100n        X7R        100n ±10% 50V X7R  Würth Elektronik                                       885012206095                                 ±10%      100n ±10% 50V X7R 50V                     
C207 47n ±10% 50V X7R  C(47NF,50V,0603)       C0603              Robotics Erlangen Capacitor Library                      47n         X7R        47n ±10%  50V X7R  Würth Elektronik                                       885012206093                                 ±10%      47n ±10% 50V X7R  50V                     
D101 150066M153000     150066M153000          WL-SFCX_0606       WL-SFCD SMD Full-color Chip LED Diffused                                                           Würth Elektronik                                       150066M153000                                                                                    
F201 5A                0157005.DRT            157T               157T Series - Standard Nano2&reg; Fuse and Clip Assembly                                           Littelfuse         576-0157005.DRT                     0157005.DRT                                                                                      
J201 61302221121       61302221121            61302221121                                                                                                           Würth Elektronik                                       61302221121                                                                                      
J202 61301821121       61301821121            61301821121                                                                                                           Würth Elektronik                                       61301821121                                                                                      
L201 742792692         742792692              WE-CBF_0603(W=2.6) WE-CBF SMD EMI Suppression Ferrite Bead                                                            Würth Elektronik                                       742792692                                                                                        
L202                   WE-GFH_4532_7447669212 WE-GFH_4532        SMD RF Choke WE-GFH                                                                                                                                                                                                                        7447669212/120uH
Q201 BSS123            BSS123                 SOT23              N-CHANNEL MOS FET                                                                                                                                                          21                                                                              
R101 1k ±1% 75V 0.1W   R(1.0K,75V,0.1W,0603)  R0603              Robotics Erlangen Resistor Library                                              1k ±1%    75V 0.1W YAGEO                                                  RC0603FR-071KL              0.1W  1k         ±1%       1k ±1% 75V 0.1W   75V                     
R102 10k ±1% 75V 0.1W  R(10K,75V,0.1W,0603)   R0603              Robotics Erlangen Resistor Library                                              10k ±1%   75V 0.1W YAGEO                                                  RC0603FR-0710KL             0.1W  10k        ±1%       10k ±1% 75V 0.1W  75V                     
R103 1k ±1% 75V 0.1W   R(1.0K,75V,0.1W,0603)  R0603              Robotics Erlangen Resistor Library                                              1k ±1%    75V 0.1W YAGEO                                                  RC0603FR-071KL              0.1W  1k         ±1%       1k ±1% 75V 0.1W   75V                     
R104 2k2 ±1% 75V 0.1W  R(2.2K,75V,0.1W,0603)  R0603              Robotics Erlangen Resistor Library                                              2k2 ±1%   75V 0.1W YAGEO                                                  RC0603FR-072K2L             0.1W  2k2        ±1%       2k2 ±1% 75V 0.1W  75V                     
R105 1k ±1% 75V 0.1W   R(1.0K,75V,0.1W,0603)  R0603              Robotics Erlangen Resistor Library                                              1k ±1%    75V 0.1W YAGEO                                                  RC0603FR-071KL              0.1W  1k         ±1%       1k ±1% 75V 0.1W   75V                     
R106 1k ±1% 75V 0.1W   R(1.0K,75V,0.1W,0603)  R0603              Robotics Erlangen Resistor Library                                              1k ±1%    75V 0.1W YAGEO                                                  RC0603FR-071KL              0.1W  1k         ±1%       1k ±1% 75V 0.1W   75V                     
R107 1k ±1% 75V 0.1W   R(1.0K,75V,0.1W,0603)  R0603              Robotics Erlangen Resistor Library                                              1k ±1%    75V 0.1W YAGEO                                                  RC0603FR-071KL              0.1W  1k         ±1%       1k ±1% 75V 0.1W   75V                     
R201 56R ±1% 75V 0.1W  R(56R,75V,0.1W,0603)   R0603              Robotics Erlangen Resistor Library                                              56R ±1%   75V 0.1W YAGEO                                                  RC0603FR-0756RL             0.1W  56R        ±1%       56R ±1% 75V 0.1W  75V                     
R202 100R ±1% 75V 0.1W R(100R,75V,0.1W,0603)  R0603              Robotics Erlangen Resistor Library                                              100R ±1%  75V 0.1W YAGEO                                                  RC0603FR-07100RL            0.1W  100R       ±1%       100R ±1% 75V 0.1W 75V                     
U101 STM32F303CC       STM32F303CC            LQFP48             Cortex M4 Microcontroller                                                                          STMicroelectronics 511-STM32F303CCT6                   STM32F303CCT6                                                                                    
U102 SN74AHC1G125DBVR  SN74AHC1G125DBVR       SOT23-5                                                                                                               Texas Instruments  595-SN74AHC1G125DBVR                SN74AHC1G125DBVR                                                                                 
U201 SN74LVC2G34       SN74LVC2G34            SOT                1. Features:                                                                                       Texas Instruments  595-SN74LVC2G34DRLR                 SN74LVC2G34                                                                                      
U202 SN74LVC2G34       SN74LVC2G34            SOT                1. Features:                                                                                       Texas Instruments  595-SN74LVC2G34DRLR                 SN74LVC2G34                                                                                      
U203 FIN1002           FIN1002                SOT23-5            3.3V LVDS 1-Bit High Speed Differential Receiver                                                                                           512-FIN1002M5X
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

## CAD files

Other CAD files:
pasta/mechanics/Wheel/assembly_drawings/FK_plunger_assembly.dwg
pasta/mechanics/Wheel/assembly_drawings/WH_assembly_pos1.dwg
pasta/mechanics/Wheel/assembly_drawings/FK_Assembly_2.dwg
pasta/mechanics/Kick/drawings/FK_assembly.dwg
pasta/mechanics/Chassis/drawings/ch_baseplate.dwg
pasta/mechanics/Dribbler/assembly_drawing/Dribbler.dwg
pasta/mechanics/Dribbler/drawings/DR_Suspension_right.dwg
pasta/mechanics/Kick/drawings/FK_plunger_front.dwg
pasta/mechanics/Object_data/Robot_2022_with_cover.obj
pasta/mechanics/STEP/Robot_2023.stp
pasta/mechanics/Wheel/drawings/WH_Motormount_pos1.dwg
pasta/mechanics/Wheel/Encoder/2018-05_encoder.step
pasta/mechanics/Wheel/WH_bearing/inafag_625-2z.stp
pasta/mechanics/Wheel/Zahnrad_Konstruktionsassistent/wheelgear.dwg
pasta/mechanics/Dribbler/drawings/DR_Panel_right.dwg
pasta/mechanics/Kick/drawings/FK_backmount.dwg
pasta/mechanics/Object_data/Robot_2022.obj
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

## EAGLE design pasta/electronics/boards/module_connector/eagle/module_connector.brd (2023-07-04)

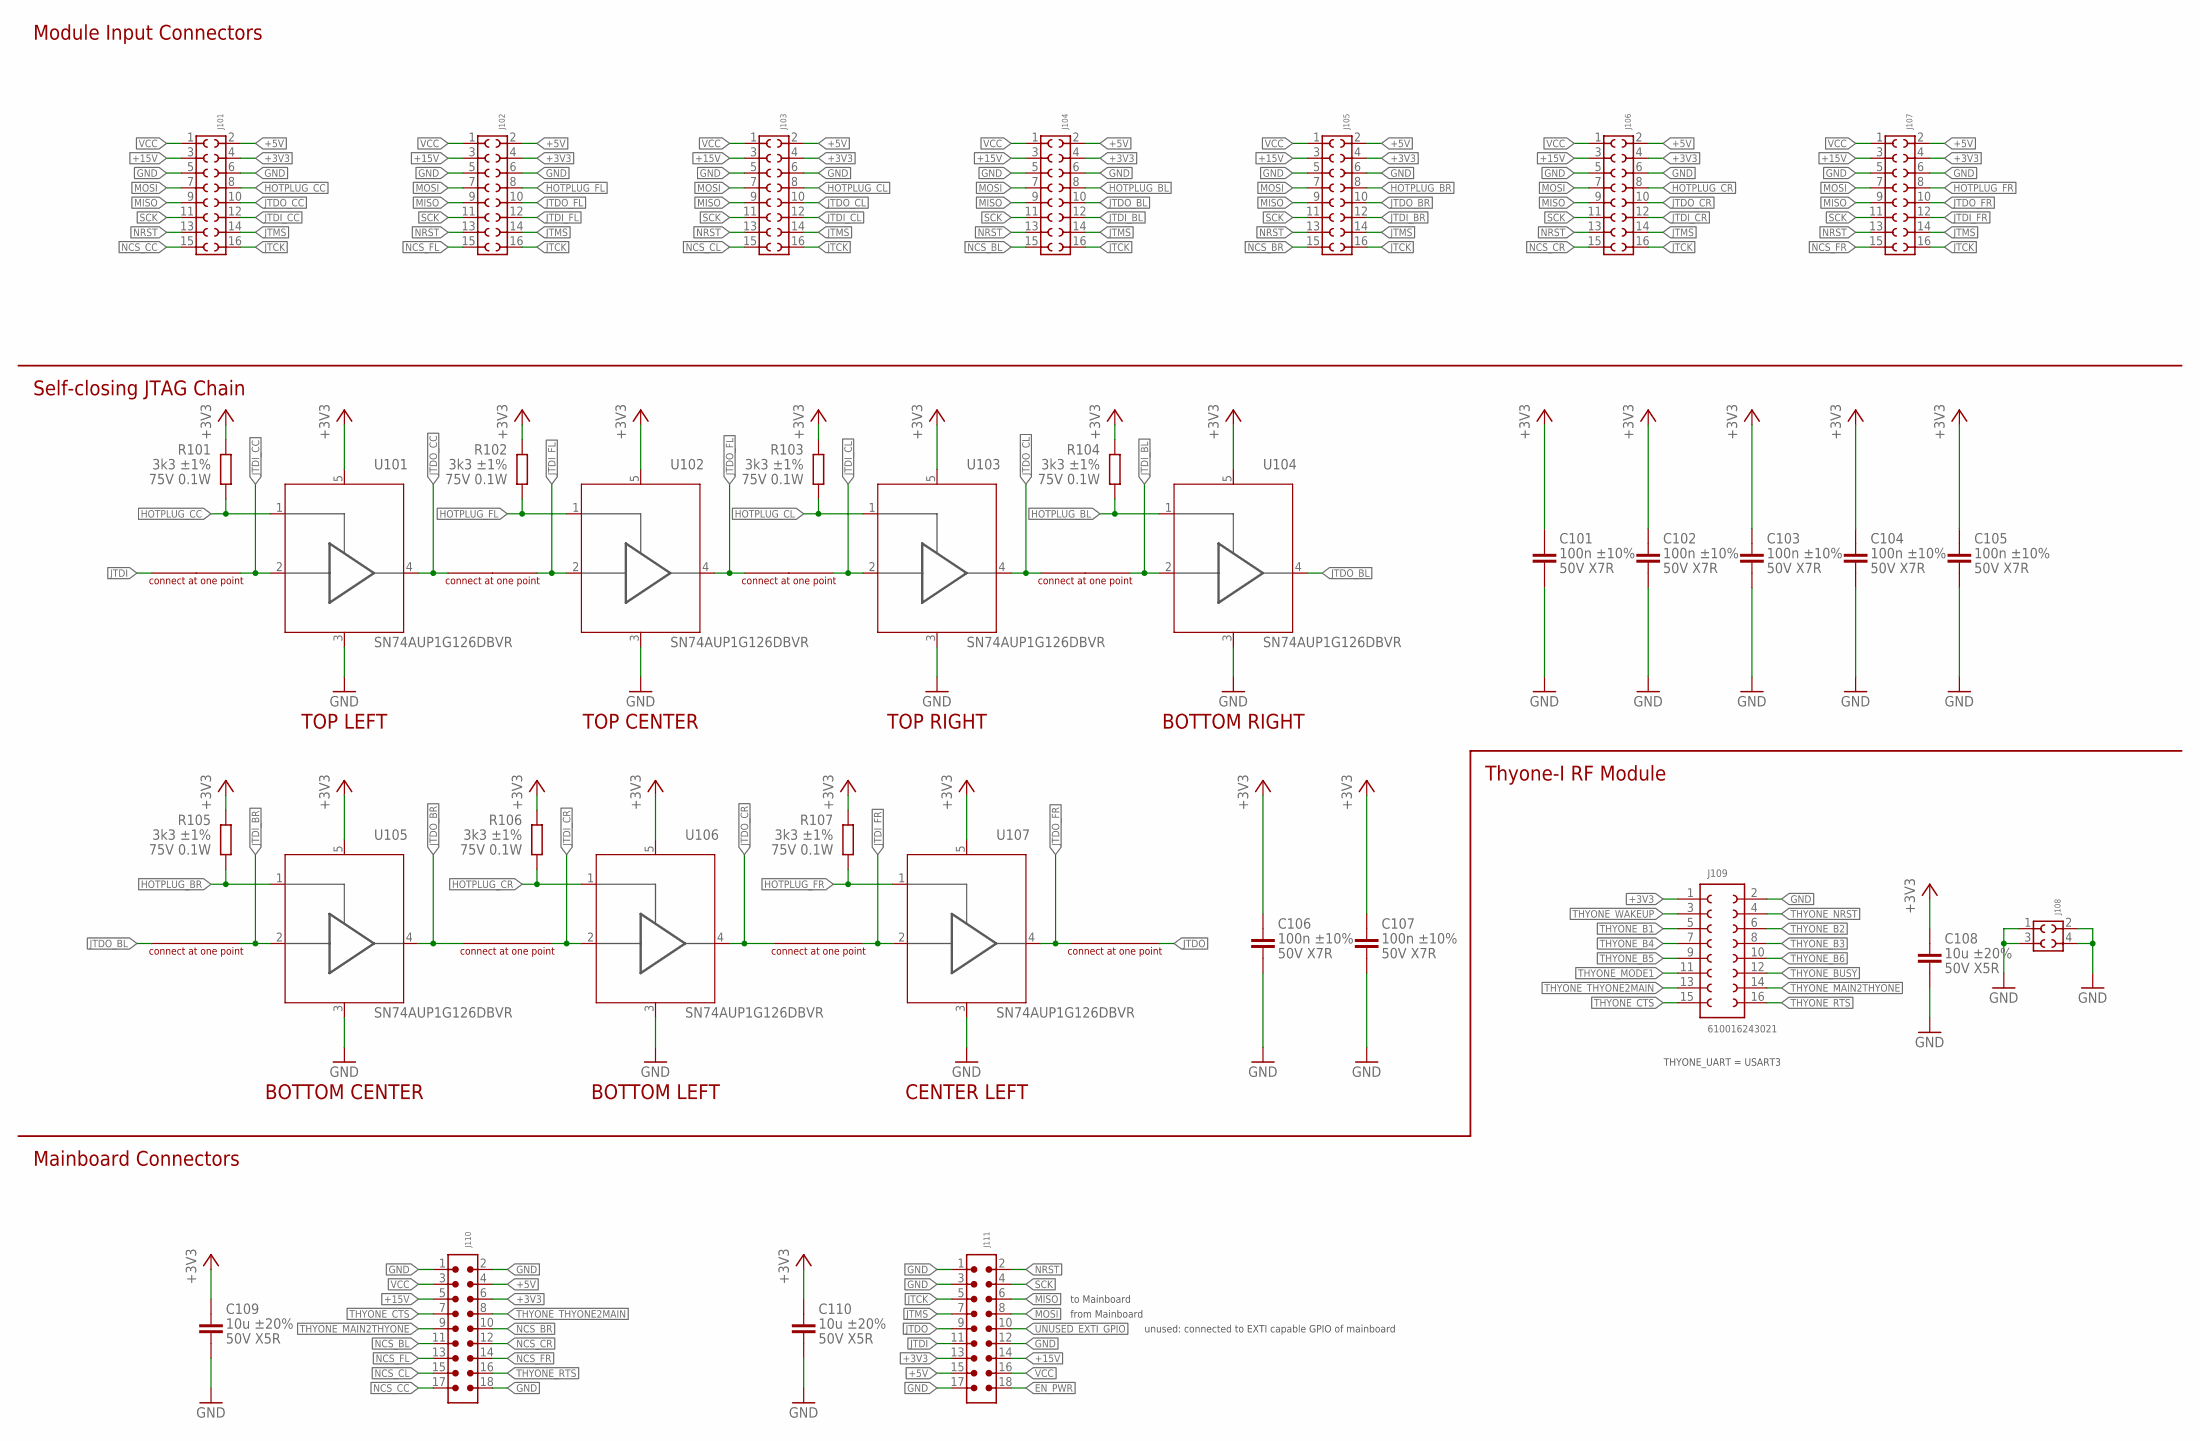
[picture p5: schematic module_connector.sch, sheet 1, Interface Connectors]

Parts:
C101, C102, C103, C104, C105, C106, C107: 100n ±10% 50V X7R; C0603
C108, C109, C110: 10u ±20% 50V X5R; C1206
J101, J102, J103, J104, J105, J106, J107: 6100XX243021_610016243021; 610016243021
J108: 6100XX243021_610004243021; 610004243021
J109: 610016243021; 610X16243021
J110, J111: 6130XX21121_61301821121; 61301821121
R101, R102, R103, R104, R105, R106, R107: 3k3 ±1% 75V 0.1W; R0603
SHORT101, SHORT102, SHORT103, SHORT104, SHORT105, SHORT106, SHORT107, SHORT108: SHORT0.254
U101, U102, U103, U104, U105, U106, U107: SN74AUP1G126DBVR; SOT23-5

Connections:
+3V3: C101.1, C102.1, C103.1, C104.1, C105.1, C106.1, C107.1, C108.1, C109.1, C110.1, J101.4, J102.4, J103.4, J104.4, J105.4, J106.4, J107.4, J109.1, J110.6, J111.13, R101.2, R102.2, R103.2, R104.2, R105.2, R106.2, R107.2, U101.5 (VCC), U102.5 (VCC), U103.5 (VCC), U104.5 (VCC), U105.5 (VCC), U106.5 (VCC), U107.5 (VCC)
+5V: J101.2, J102.2, J103.2, J104.2, J105.2, J106.2, J107.2, J110.4, J111.15
+15V: J101.3, J102.3, J103.3, J104.3, J105.3, J106.3, J107.3, J110.5, J111.14
EN_PWR: J111.18
GND: C101.2, C102.2, C103.2, C104.2, C105.2, C106.2, C107.2, C108.2, C109.2, C110.2, J101.5, J101.6, J102.5, J102.6, J103.5, J103.6, J104.5, J104.6, J105.5, J105.6, J106.5, J106.6, J107.5, J107.6, J108.1, J108.2, J108.3, J108.4, J109.2 (16), J110.1, J110.2, J110.18, J111.1, J111.3, J111.12, J111.17, U101.3 (GND), U102.3 (GND), U103.3 (GND), U104.3 (GND), U105.3 (GND), U106.3 (GND), U107.3 (GND)
HOTPLUG_BL: J104.8, R104.1, U104.1 (OE)
HOTPLUG_BR: J105.8, R105.1, U105.1 (OE)
HOTPLUG_CC: J101.8, R101.1, U101.1 (OE)
HOTPLUG_CL: J103.8, R103.1, U103.1 (OE)
HOTPLUG_CR: J106.8, R106.1, U106.1 (OE)
HOTPLUG_FL: J102.8, R102.1, U102.1 (OE)
HOTPLUG_FR: J107.8, R107.1, U107.1 (OE)
JTCK: J101.16, J102.16, J103.16, J104.16, J105.16, J106.16, J107.16, J111.5
JTDI: J111.11, SHORT101.P1
JTDI_BL: J104.12, SHORT104.P2, U104.2 (I)
JTDI_BR: J105.12, SHORT105.P2, U105.2 (I)
JTDI_CC: J101.12, SHORT101.P2, U101.2 (I)
JTDI_CL: J103.12, SHORT103.P2, U103.2 (I)
JTDI_CR: J106.12, SHORT106.P2, U106.2 (I)
JTDI_FL: J102.12, SHORT102.P2, U102.2 (I)
JTDI_FR: J107.12, SHORT107.P2, U107.2 (I)
JTDO: J111.9, SHORT108.P2
JTDO_BL: J104.10, SHORT105.P1, U104.4 (O)
JTDO_BR: J105.10, SHORT106.P1, U105.4 (O)
JTDO_CC: J101.10, SHORT102.P1, U101.4 (O)
JTDO_CL: J103.10, SHORT104.P1, U103.4 (O)
JTDO_CR: J106.10, SHORT107.P1, U106.4 (O)
JTDO_FL: J102.10, SHORT103.P1, U102.4 (O)
JTDO_FR: J107.10, SHORT108.P1, U107.4 (O)
JTMS: J101.14, J102.14, J103.14, J104.14, J105.14, J106.14, J107.14, J111.7
MISO: J101.9, J102.9, J103.9, J104.9, J105.9, J106.9, J107.9, J111.6
MOSI: J101.7, J102.7, J103.7, J104.7, J105.7, J106.7, J107.7, J111.8
NCS_BL: J104.15, J110.11
NCS_BR: J105.15, J110.10
NCS_CC: J101.15, J110.17
NCS_CL: J103.15, J110.15
NCS_CR: J106.15, J110.12
NCS_FL: J102.15, J110.13
NCS_FR: J107.15, J110.14
NRST: J101.13, J102.13, J103.13, J104.13, J105.13, J106.13, J107.13, J111.2
SCK: J101.11, J102.11, J103.11, J104.11, J105.11, J106.11, J107.11, J111.4
THYONE_B1: J109.5 (3)
THYONE_B2: J109.6 (14)
THYONE_B3: J109.8 (13)
THYONE_B4: J109.7 (4)
THYONE_B5: J109.9 (5)
THYONE_B6: J109.10 (12)
THYONE_BUSY: J109.12 (11)
THYONE_CTS: J109.15 (8), J110.7
THYONE_MAIN2THYONE: J109.14 (10), J110.9
THYONE_MODE1: J109.11 (6)
THYONE_NRST: J109.4 (15)
THYONE_RTS: J109.16 (9), J110.16
THYONE_THYONE2MAIN: J109.13 (7), J110.8
THYONE_WAKEUP: J109.3 (2)
UNUSED_EXTI_GPIO: J111.10
VCC: J101.1, J102.1, J103.1, J104.1, J105.1, J106.1, J107.1, J110.3, J111.16

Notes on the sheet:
Module Input Connectors
Self-closing JTAG Chain
TOP LEFT
TOP CENTER
TOP RIGHT
BOTTOM RIGHT
BOTTOM CENTER
BOTTOM LEFT
CENTER LEFT
Mainboard Connectors
Thyone-I RF Module
from Mainboard
to Mainboard
THYONE_UART = USART3
unused: connected to EXTI capable GPIO of mainboard

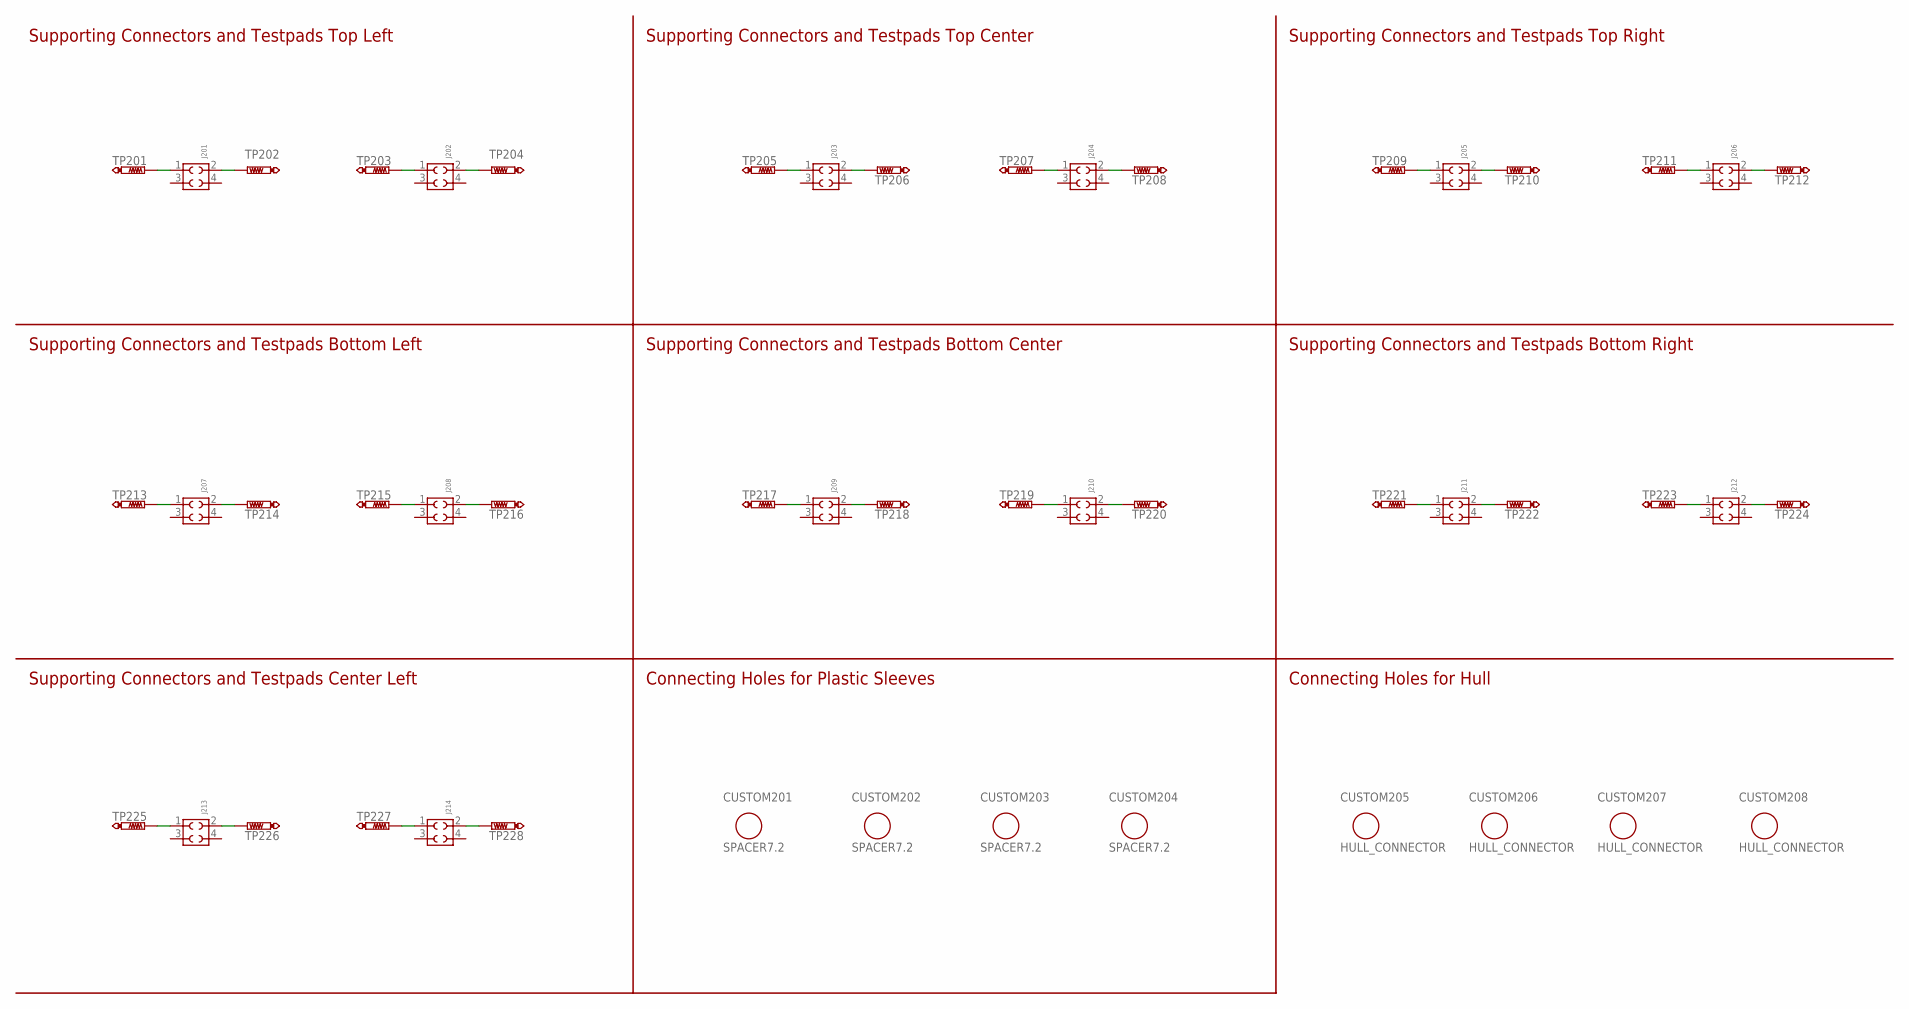
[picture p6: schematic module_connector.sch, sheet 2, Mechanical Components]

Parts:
CUSTOM201, CUSTOM202, CUSTOM203, CUSTOM204: SPACER7.2; PLASTIC_SPACER
CUSTOM205, CUSTOM206, CUSTOM207, CUSTOM208: HULL_CONNECTOR
J201, J202, J203, J204, J205, J206, J207, J208, J209, J210, J211, J212, J213, J214: 6100XX243021_610004243021; 610004243021
TP201, TP202, TP203, TP204, TP205, TP206, TP207, TP208, TP209, TP210, TP211, TP212, TP213, TP214, TP215, TP216, TP217, TP218, TP219, TP220, TP221, TP222, TP223, TP224, TP225, TP226, TP227, TP228: TESTPAD

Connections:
unnamed: J201.1, TP201.P$1
unnamed: J201.2, TP202.P$1
unnamed: J203.1, TP205.P$1
unnamed: J203.2, TP206.P$1
unnamed: J202.1, TP203.P$1
unnamed: J204.1, TP207.P$1
unnamed: J202.2, TP204.P$1
unnamed: J204.2, TP208.P$1
unnamed: J205.1, TP209.P$1
unnamed: J205.2, TP210.P$1
unnamed: J206.1, TP211.P$1
unnamed: J206.2, TP212.P$1
unnamed: J207.1, TP213.P$1
unnamed: J207.2, TP214.P$1
unnamed: J208.1, TP215.P$1
unnamed: J208.2, TP216.P$1
unnamed: J209.1, TP217.P$1
unnamed: J209.2, TP218.P$1
unnamed: J210.1, TP219.P$1
unnamed: J210.2, TP220.P$1
unnamed: J211.1, TP221.P$1
unnamed: J211.2, TP222.P$1
unnamed: J212.1, TP223.P$1
unnamed: J212.2, TP224.P$1
unnamed: J213.1, TP225.P$1
unnamed: J213.2, TP226.P$1
unnamed: J214.1, TP227.P$1
unnamed: J214.2, TP228.P$1

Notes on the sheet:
Supporting Connectors and Testpads Top Left
Supporting Connectors and Testpads Top Center
Supporting Connectors and Testpads Top Right
Supporting Connectors and Testpads Bottom Left
Supporting Connectors and Testpads Bottom Center
Supporting Connectors and Testpads Bottom Right
Supporting Connectors and Testpads Center Left
Connecting Holes for Plastic Sleeves
Connecting Holes for Hull

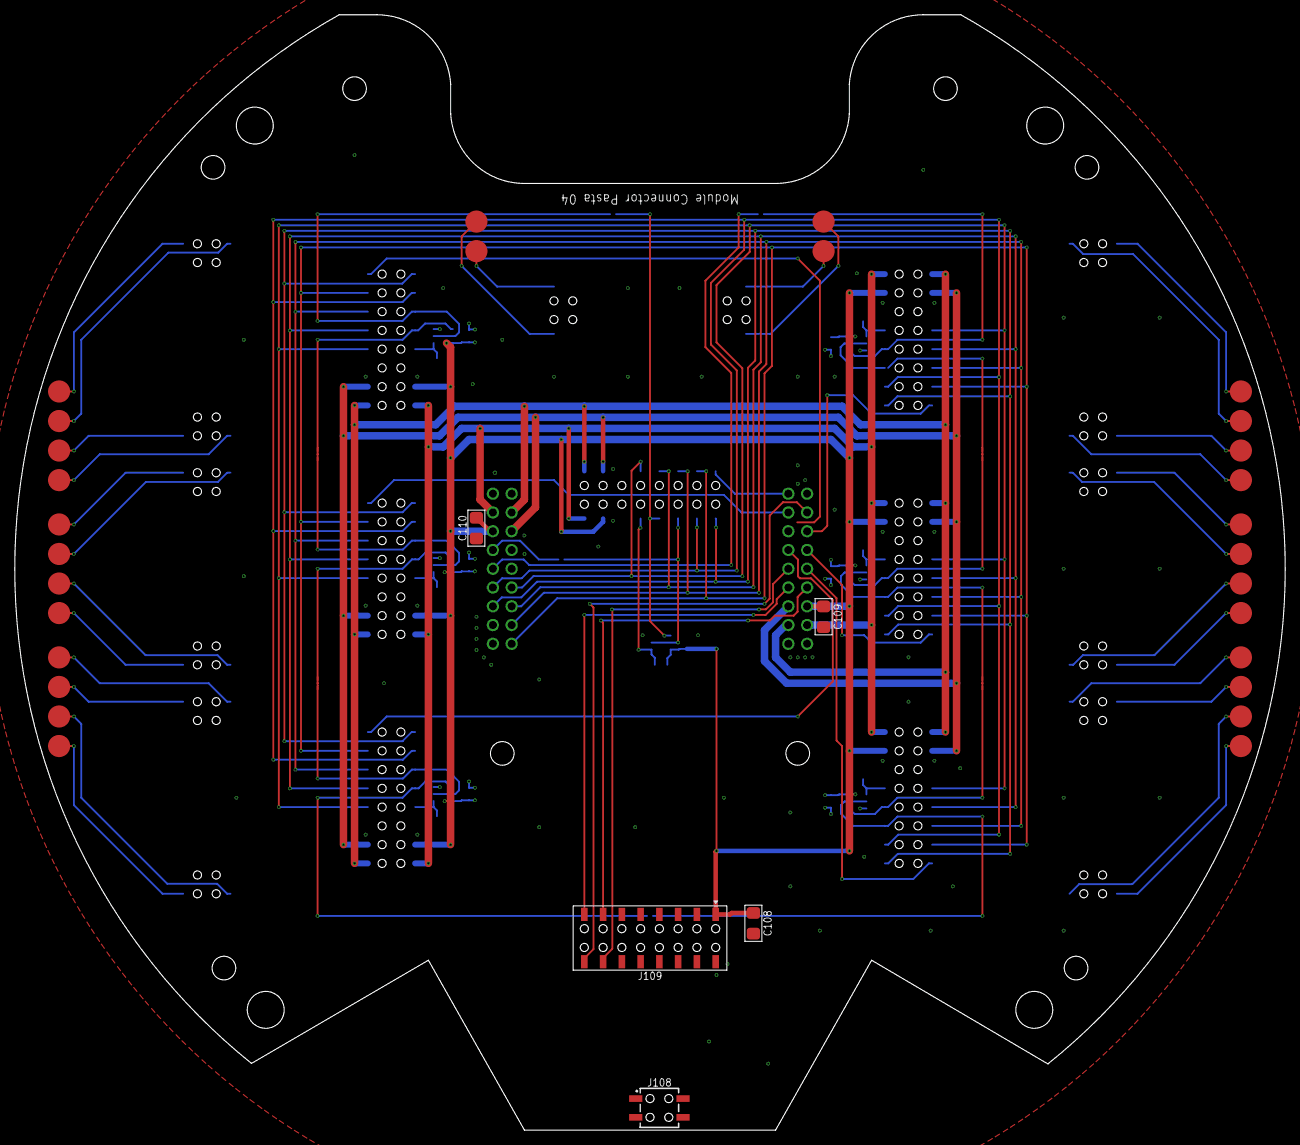
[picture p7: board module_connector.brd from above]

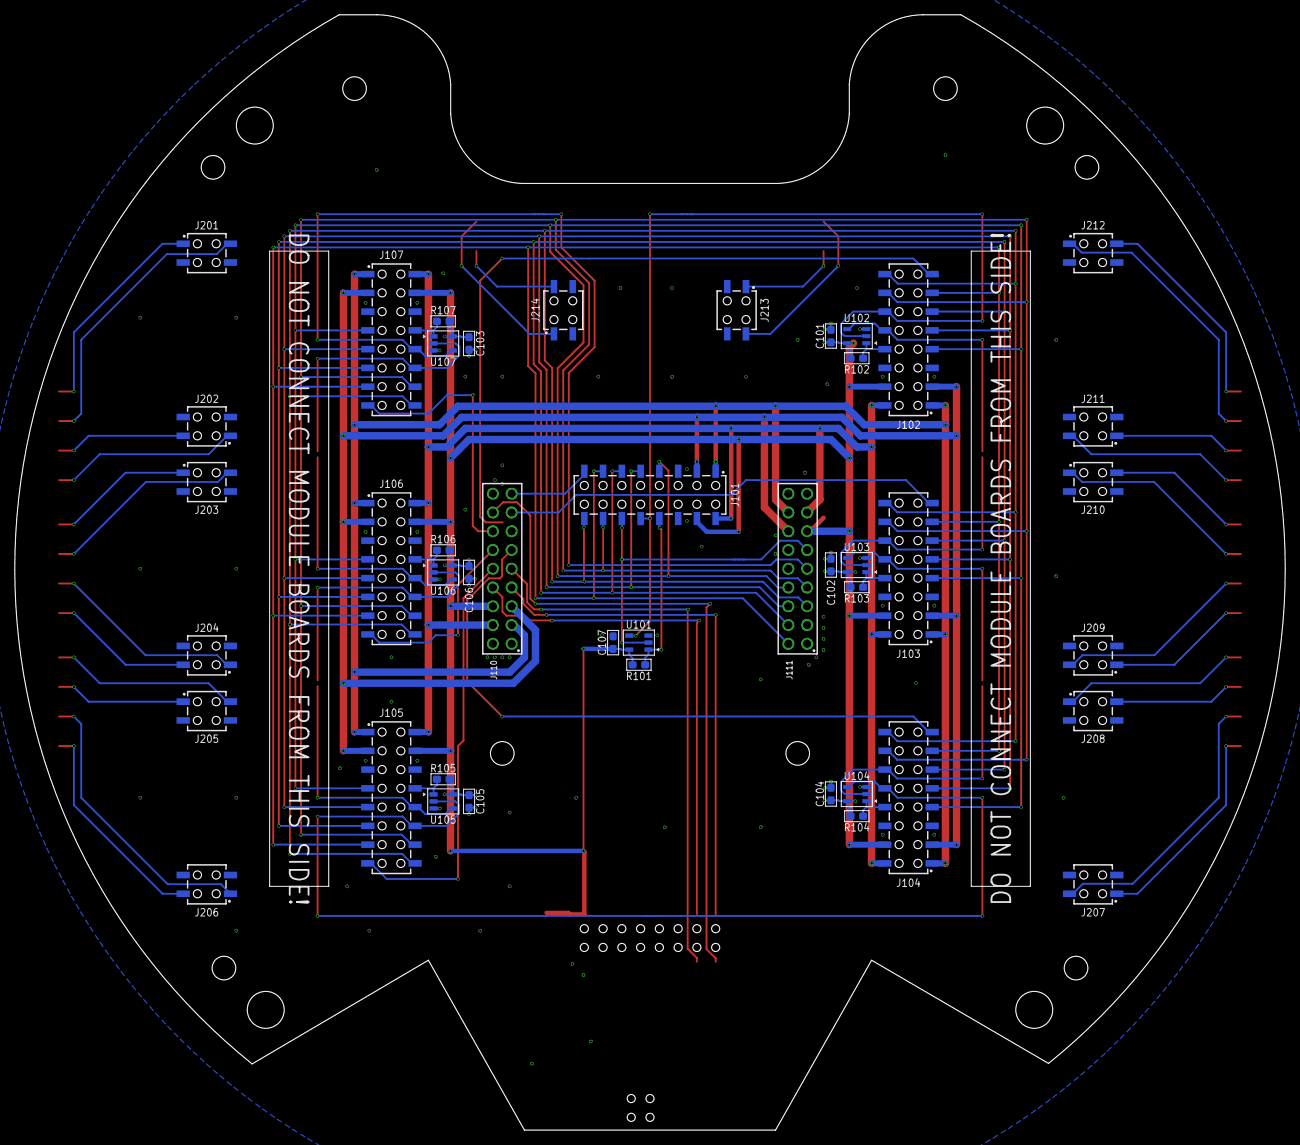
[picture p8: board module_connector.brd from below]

Board: 2 copper layers, 172.0 x 151.0 mm, 104 parts (48 on the bottom side), 73 nets.

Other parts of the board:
U$1, U$13, U$15, U$20, U$21, U$22, U$23: MODULE_BOARD
U$2: HULL
U$3: RF-MODULE
U$16, U$17: LOGO

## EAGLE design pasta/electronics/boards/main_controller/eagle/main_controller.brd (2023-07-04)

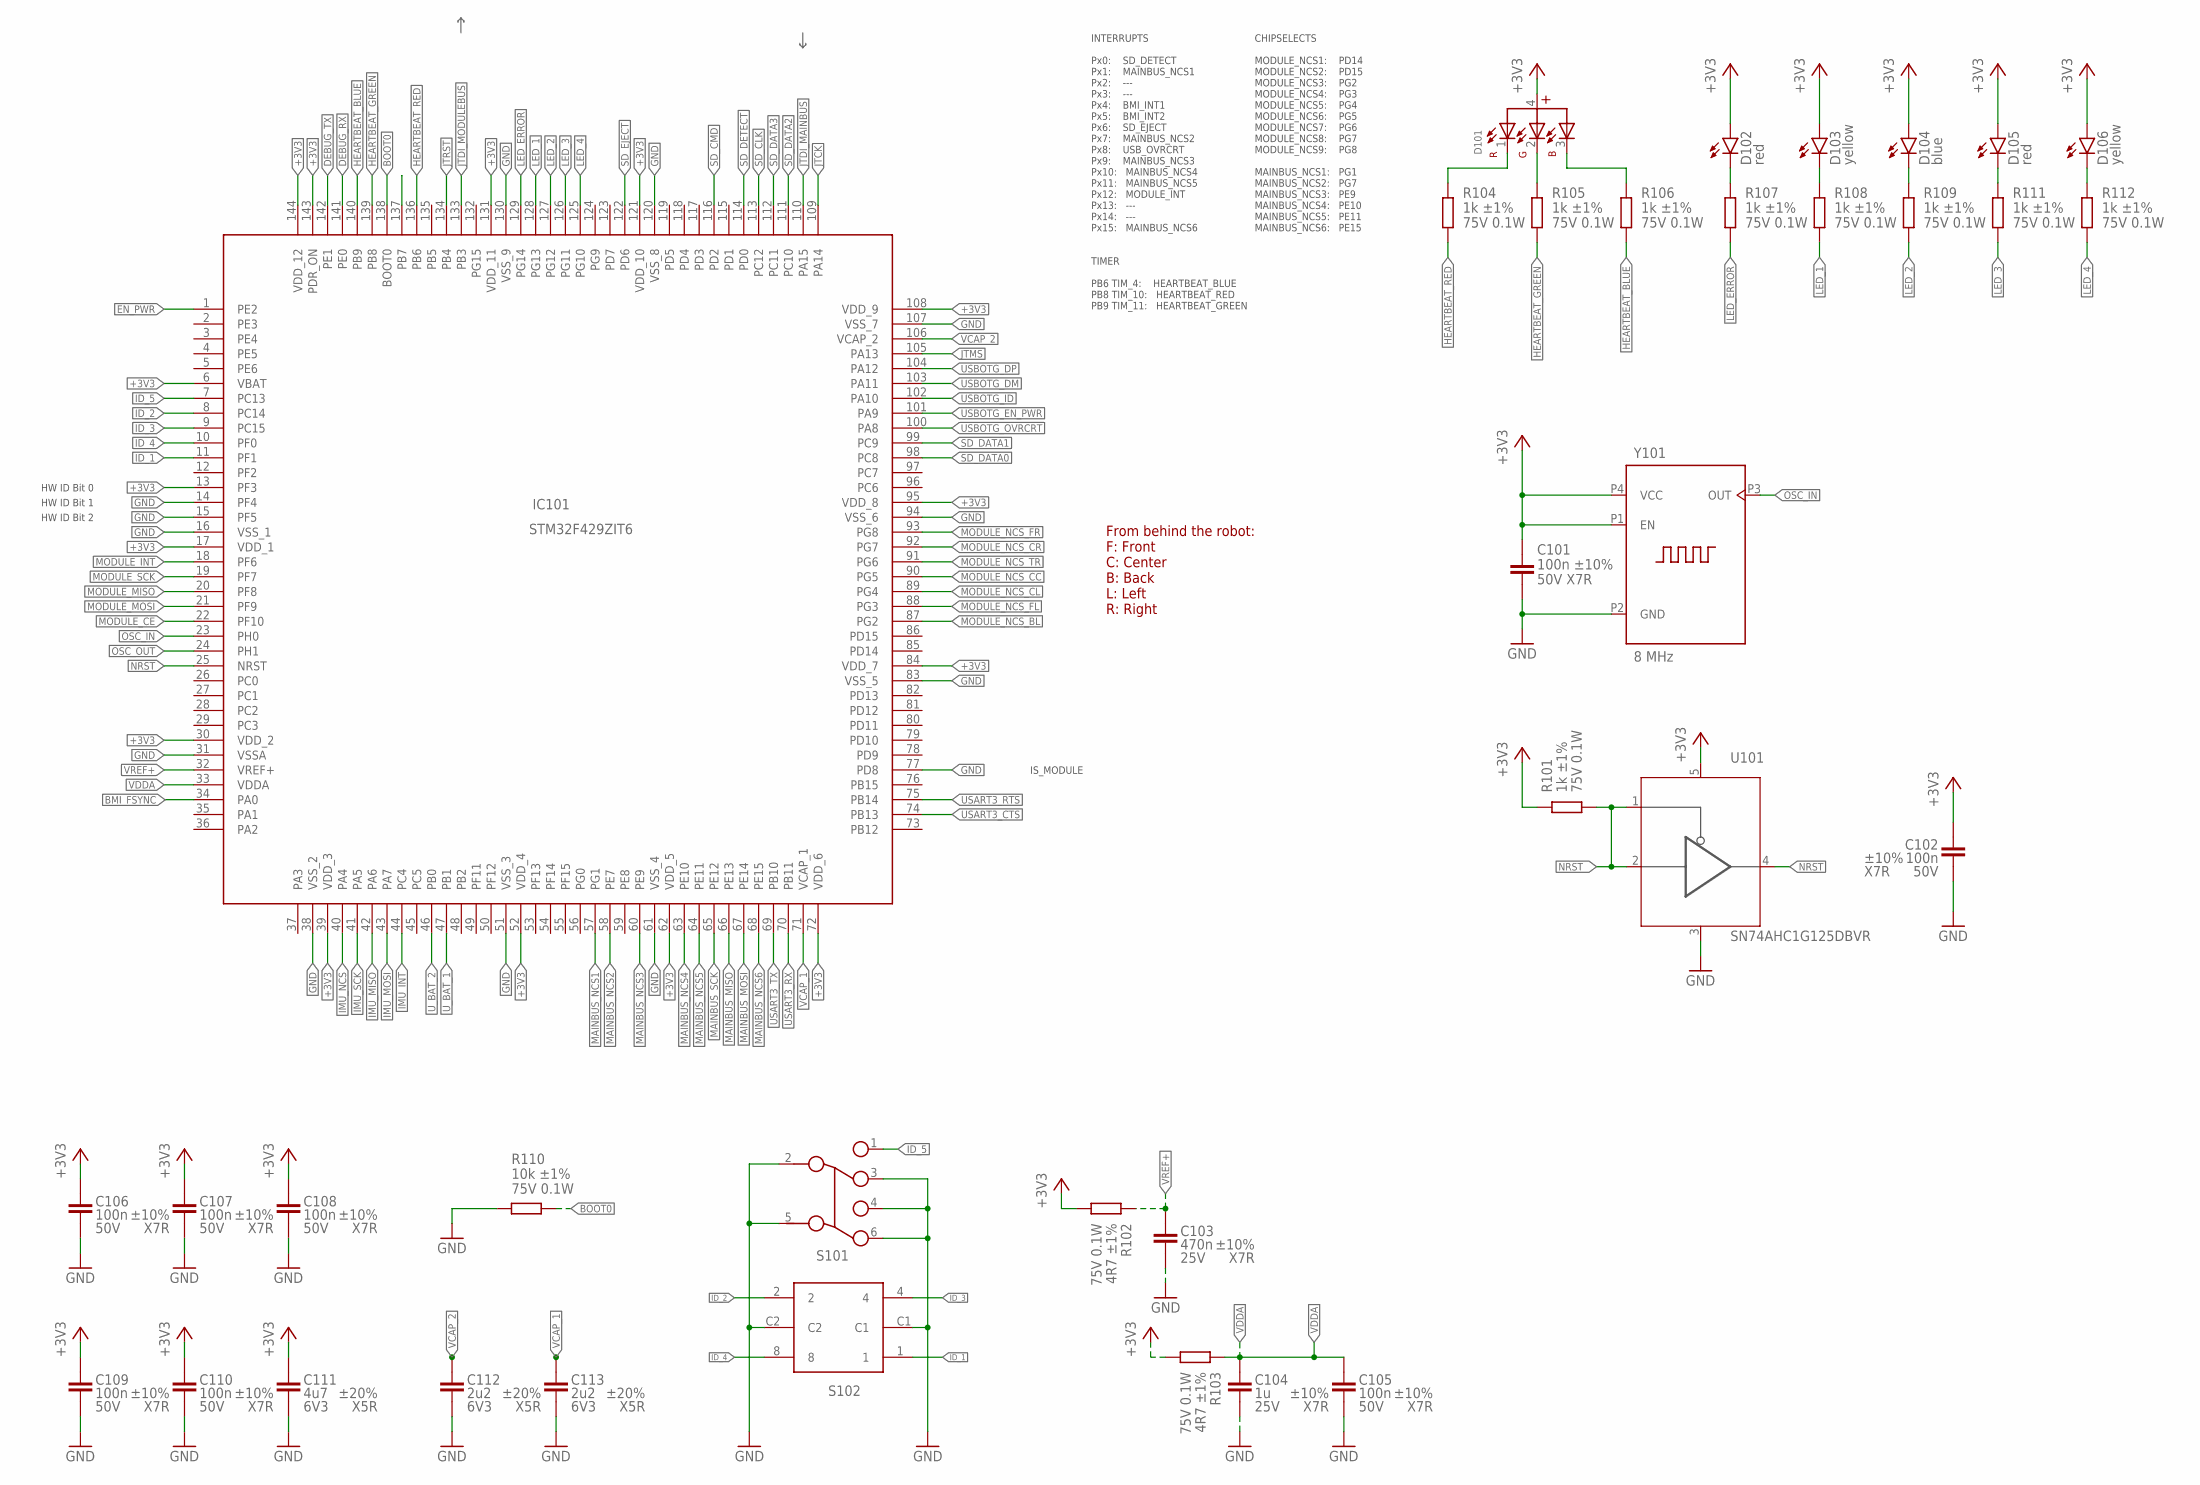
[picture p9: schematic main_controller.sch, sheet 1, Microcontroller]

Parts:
C101, C102, C105, C106, C107, C108, C109, C110: 100n ±10% 50V X7R; C0603
C103: 470n ±10% 25V X7R; C0603
C104: 1u ±10% 25V X7R; C0603
C111: 4u7 ±20% 6V3 X5R; C0603
C112, C113: 2u2 ±20% 6V3 X5R; C0603
D101: WL-SFCD_0606_150066M153000; WL-SFCX_0606
D102, D105: red; CHIPLED_0805
D103, D106: yellow; CHIPLED_0805
D104: blue; CHIPLED_0805
IC101: STM32F429ZIT6; QFP50P2200X2200X160-144N
R101, R104, R105, R106, R107, R108, R109, R111, R112: 1k ±1% 75V 0.1W; R0603
R102, R103: 4R7 ±1% 75V 0.1W; R0603
R110: 10k ±1% 75V 0.1W; R0603
S101: 452403012014
S102: 428542320816
U101: SN74AHC1G125DBVR; SOT23-5
Y101: 8 MHz; 830207192009

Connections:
+3V3: C101.1, C102.1, C106.1, C107.1, C108.1, C109.1, C110.1, C111.1, D101.4, D102.A, D103.A, D104.A, D105.A, D106.A, IC101.6 (VBAT), IC101.13 (PF3), IC101.17 (VDD_1), IC101.30 (VDD_2), IC101.39 (VDD_3), IC101.52 (VDD_4), IC101.62 (VDD_5), IC101.72 (VDD_6), IC101.84 (VDD_7), IC101.95 (VDD_8), IC101.108 (VDD_9), IC101.121 (VDD_10), IC101.131 (VDD_11), IC101.143 (PDR_ON), IC101.144 (VDD_12), R101.2, R102.1, R103.1, U101.5 (VCC), Y101.P1 (EN), Y101.P4 (VCC); also elsewhere on the board
BMI_FSYNC: IC101.34 (PA0); also elsewhere on the board
BOOT0: IC101.138 (BOOT0), R110.1
DEBUG_RX: IC101.141 (PE0); also elsewhere on the board
DEBUG_TX: IC101.142 (PE1); also elsewhere on the board
EN_PWR: IC101.1 (PE2); also elsewhere on the board
GND: C101.2, C102.2, C103.2, C104.2, C105.2, C106.2, C107.2, C108.2, C109.2, C110.2, C111.2, C112.2, C113.2, IC101.14 (PF4), IC101.15 (PF5), IC101.16 (VSS_1), IC101.31 (VSSA), IC101.38 (VSS_2), IC101.51 (VSS_3), IC101.61 (VSS_4), IC101.77 (PD8), IC101.83 (VSS_5), IC101.94 (VSS_6), IC101.107 (VSS_7), IC101.120 (VSS_8), IC101.130 (VSS_9), R110.2, S101.2, S101.3, S101.4, S101.5, S101.6, S102.C1, S102.C2, U101.3 (GND), Y101.P2 (GND); also elsewhere on the board
HEARTBEAT_BLUE: IC101.140 (PB9), R106.1
HEARTBEAT_GREEN: IC101.139 (PB8), R105.1
HEARTBEAT_RED: IC101.136 (PB6), R104.1
ID_1: IC101.11 (PF1), S102.1
ID_2: IC101.8 (PC14), S102.2
ID_3: IC101.9 (PC15), S102.4
ID_4: IC101.10 (PF0), S102.8
ID_5: IC101.7 (PC13), S101.1
IMU_INT: IC101.44 (PC4); also elsewhere on the board
IMU_MISO: IC101.42 (PA6); also elsewhere on the board
IMU_MOSI: IC101.43 (PA7); also elsewhere on the board
IMU_NCS: IC101.40 (PA4); also elsewhere on the board
IMU_SCK: IC101.41 (PA5); also elsewhere on the board
JTCK: IC101.109 (PA14); also elsewhere on the board
JTDI_MAINBUS: IC101.110 (PA15); also elsewhere on the board
JTDI_MODULEBUS: IC101.133 (PB3); also elsewhere on the board
JTMS: IC101.105 (PA13); also elsewhere on the board
JTRST: IC101.134 (PB4)
LED_1: IC101.128 (PG13), R108.1
LED_2: IC101.127 (PG12), R109.1
LED_3: IC101.126 (PG11), R111.1
LED_4: IC101.125 (PG10), R112.1
LED_ERROR: IC101.129 (PG14), R107.1
MAINBUS_MISO: IC101.66 (PE13); also elsewhere on the board
MAINBUS_MOSI: IC101.67 (PE14); also elsewhere on the board
MAINBUS_NCS1: IC101.57 (PG1); also elsewhere on the board
MAINBUS_NCS2: IC101.58 (PE7); also elsewhere on the board
MAINBUS_NCS3: IC101.60 (PE9); also elsewhere on the board
MAINBUS_NCS4: IC101.63 (PE10); also elsewhere on the board
MAINBUS_NCS5: IC101.64 (PE11); also elsewhere on the board
MAINBUS_NCS6: IC101.68 (PE15); also elsewhere on the board
MAINBUS_SCK: IC101.65 (PE12); also elsewhere on the board
MODULE_CE: IC101.22 (PF10)
MODULE_INT: IC101.18 (PF6); also elsewhere on the board
MODULE_MISO: IC101.20 (PF8); also elsewhere on the board
MODULE_MOSI: IC101.21 (PF9); also elsewhere on the board
MODULE_NCS_BL: IC101.87 (PG2); also elsewhere on the board
MODULE_NCS_CC: IC101.90 (PG5); also elsewhere on the board
MODULE_NCS_CL: IC101.89 (PG4); also elsewhere on the board
MODULE_NCS_CR: IC101.92 (PG7); also elsewhere on the board
MODULE_NCS_FL: IC101.88 (PG3); also elsewhere on the board
MODULE_NCS_FR: IC101.93 (PG8); also elsewhere on the board
MODULE_NCS_TR: IC101.91 (PG6); also elsewhere on the board
MODULE_SCK: IC101.19 (PF7); also elsewhere on the board
unnamed: D102.C, R107.2
unnamed: D103.C, R108.2
unnamed: D104.C, R109.2
unnamed: D101.1 (R), R104.2
unnamed: D101.2 (G), R105.2
unnamed: D101.3 (B), R106.2
unnamed: D105.C, R111.2
unnamed: D106.C, R112.2
NRST: IC101.25 (NRST), U101.4 (O); also elsewhere on the board
NRST_: R101.1, U101.1 (OE), U101.2 (I); also elsewhere on the board
OSC_IN: IC101.23 (PH0), Y101.P3 (OUT)
OSC_OUT: IC101.24 (PH1)
SD_CLK: IC101.113 (PC12); also elsewhere on the board
SD_CMD: IC101.116 (PD2); also elsewhere on the board
SD_DATA0: IC101.98 (PC8); also elsewhere on the board
SD_DATA1: IC101.99 (PC9); also elsewhere on the board
SD_DATA2: IC101.111 (PC10); also elsewhere on the board
SD_DATA3: IC101.112 (PC11); also elsewhere on the board
SD_DETECT: IC101.114 (PD0); also elsewhere on the board
SD_EJECT: IC101.122 (PD6); also elsewhere on the board
USART3_CTS: IC101.74 (PB13); also elsewhere on the board
USART3_RTS: IC101.75 (PB14); also elsewhere on the board
USART3_RX: IC101.70 (PB11); also elsewhere on the board
USART3_TX: IC101.69 (PB10); also elsewhere on the board
USBOTG_DM: IC101.103 (PA11); also elsewhere on the board
USBOTG_DP: IC101.104 (PA12); also elsewhere on the board
USBOTG_EN_PWR: IC101.101 (PA9); also elsewhere on the board
USBOTG_ID: IC101.102 (PA10)
USBOTG_OVRCRT: IC101.100 (PA8); also elsewhere on the board
U_BAT_1: IC101.47 (PB1); also elsewhere on the board
U_BAT_2: IC101.46 (PB0); also elsewhere on the board
VCAP_1: C113.1, IC101.71 (VCAP_1)
VCAP_2: C112.1, IC101.106 (VCAP_2)
VDDA: C104.1, C105.1, IC101.33 (VDDA), R103.2
VREF+: C103.1, IC101.32 (VREF+), R102.2

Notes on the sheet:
HW ID Bit 0
HW ID Bit 1
HW ID Bit 2
IS_MODULE
INTERRUPTS Px0: SD_DETECT Px1: MAINBUS_NCS1 Px2: --- Px3: --- Px4: BMI_INT1 Px5: BMI_INT2 Px6: SD_EJECT Px7: MAINBUS_NCS2 Px8: USB_OVRCRT Px9: MAINBUS_NCS3 Px10: MAINBUS_NCS4 Px11: MAINBUS_NCS5 Px12: MODULE_INT Px13: --- Px14: --- Px15: MAINBUS_NCS6
TIMER PB6 TIM_4: HEARTBEAT_BLUE PB8 TIM_10: HEARTBEAT_RED PB9 TIM_11: HEARTBEAT_GREEN
CHIPSELECTS MODULE_NCS1: PD14 MODULE_NCS2: PD15 MODULE_NCS3: PG2 MODULE_NCS4: PG3 MODULE_NCS5: PG4 MODULE_NCS6: PG5 MODULE_NCS7: PG6 MODULE_NCS8: PG7 MODULE_NCS9: PG8 MAINBUS_NCS1: PG1 MAINBUS_NCS2: PG7 MAINBUS_NCS3: PE9 MAINBUS_NCS4: PE10 MAINBUS_NCS5: PE11 MAINBUS_NCS6: PE15
From behind the robot: F: Front C: Center B: Back L: Left R: Right

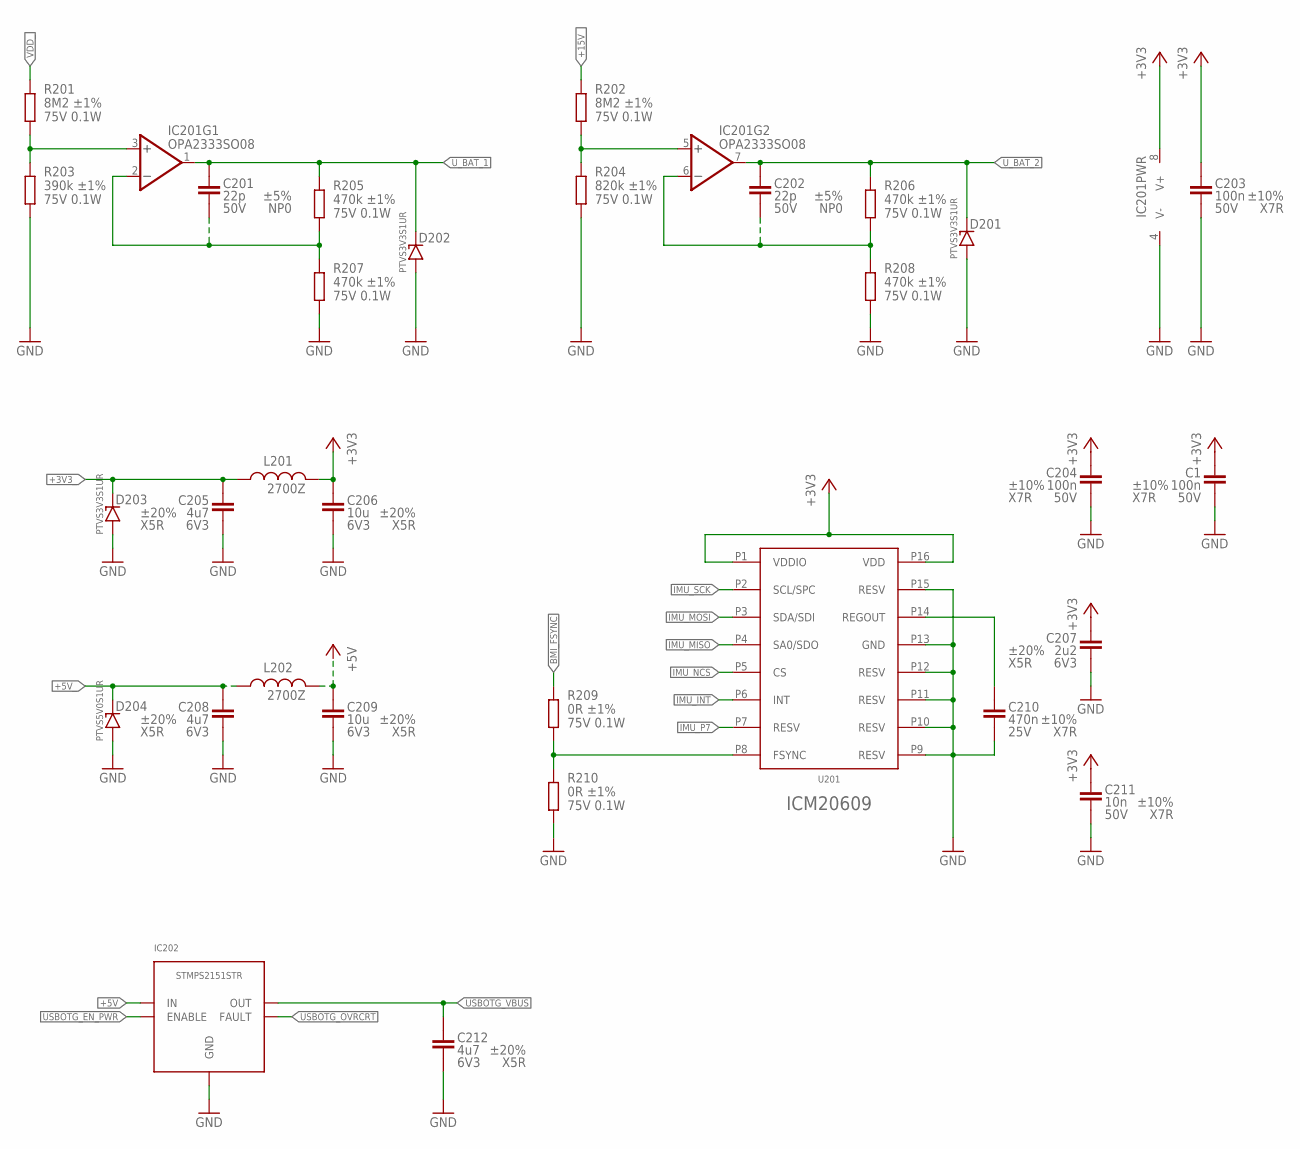
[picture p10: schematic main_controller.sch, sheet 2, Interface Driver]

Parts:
C1, C203, C204: 100n ±10% 50V X7R; C0603
C201, C202: 22p ±5% 50V NP0; C0603
C205, C208, C212: 4u7 ±20% 6V3 X5R; C0603
C206, C209: 10u ±20% 6V3 X5R; C0603
C207: 2u2 ±20% 6V3 X5R; C0603
C210: 470n ±10% 25V X7R; C0603
C211: 10n ±10% 50V X7R; C0603
D201, D202, D203: PTVS3V3S1UR; SOD123
D204: PTVS5V0S1UR; SOD123
IC201: OPA2333SO08; SO08; MPN OPA2333AIDR; MOUSER 595-OPA2333AIDR
IC202: STMPS2151STR; SOT23-5:1
L201, L202: 2700Z; WE-CBF_0603(W=2.6)
R201, R202: 8M2 ±1% 75V 0.1W; R0603
R203: 390k ±1% 75V 0.1W; R0603
R204: 820k ±1% 75V 0.1W; R0603
R205, R206, R207, R208: 470k ±1% 75V 0.1W; R0603
R209, R210: 0R ±1% 75V 0.1W; R0603
U201: ICM20609

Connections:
+3V3: C1.1, C203.1, C204.1, C206.1, C207.1, C211.1, IC201.8 (V+), L201.1, U201.P1 (VDDIO), U201.P16 (VDD); also elsewhere on the board
+3V3_: C205.1, D203.C (KATHODE), L201.2; also elsewhere on the board
+5V: C209.1, IC202.5 (IN), L202.1
+5V_: C208.1, D204.C (KATHODE), L202.2; also elsewhere on the board
+15V_: R202.2; also elsewhere on the board
BMI_FSYNC: R209.2; also elsewhere on the board
GND: C1.2, C203.2, C204.2, C205.2, C206.2, C207.2, C208.2, C209.2, C210.2, C211.2, C212.2, D201.A (ANODE), D202.A (ANODE), D203.A (ANODE), D204.A (ANODE), IC201.4 (V-), IC202.2 (GND), R203.1, R204.1, R207.1, R208.1, R210.1, U201.P9 (RESV), U201.P10 (RESV), U201.P11 (RESV), U201.P12 (RESV), U201.P13 (GND), U201.P15 (RESV); also elsewhere on the board
IMU_INT: U201.P6 (INT); also elsewhere on the board
IMU_MISO: U201.P4 (SA0/SDO); also elsewhere on the board
IMU_MOSI: U201.P3 (SDA/SDI); also elsewhere on the board
IMU_NCS: U201.P5 (CS); also elsewhere on the board
IMU_P7: U201.P7 (RESV)
IMU_SCK: U201.P2 (SCL/SPC); also elsewhere on the board
unnamed: IC201.3 (+IN), R201.1, R203.2
unnamed: C201.2, IC201.2 (-IN), R205.1, R207.2
unnamed: C202.2, IC201.6 (-IN), R206.1, R208.2
unnamed: IC201.5 (+IN), R202.1, R204.2
unnamed: R209.1, R210.2, U201.P8 (FSYNC)
unnamed: C210.1, U201.P14 (REGOUT)
USBOTG_EN_PWR: IC202.4 (ENABLE); also elsewhere on the board
USBOTG_OVRCRT: IC202.3 (FAULT); also elsewhere on the board
USBOTG_VBUS: C212.1, IC202.1 (OUT); also elsewhere on the board
U_BAT_1: C201.1, D202.C (KATHODE), IC201.1 (OUT), R205.2; also elsewhere on the board
U_BAT_2: C202.1, D201.C (KATHODE), IC201.7 (OUT), R206.2; also elsewhere on the board
VDD_: R201.2; also elsewhere on the board

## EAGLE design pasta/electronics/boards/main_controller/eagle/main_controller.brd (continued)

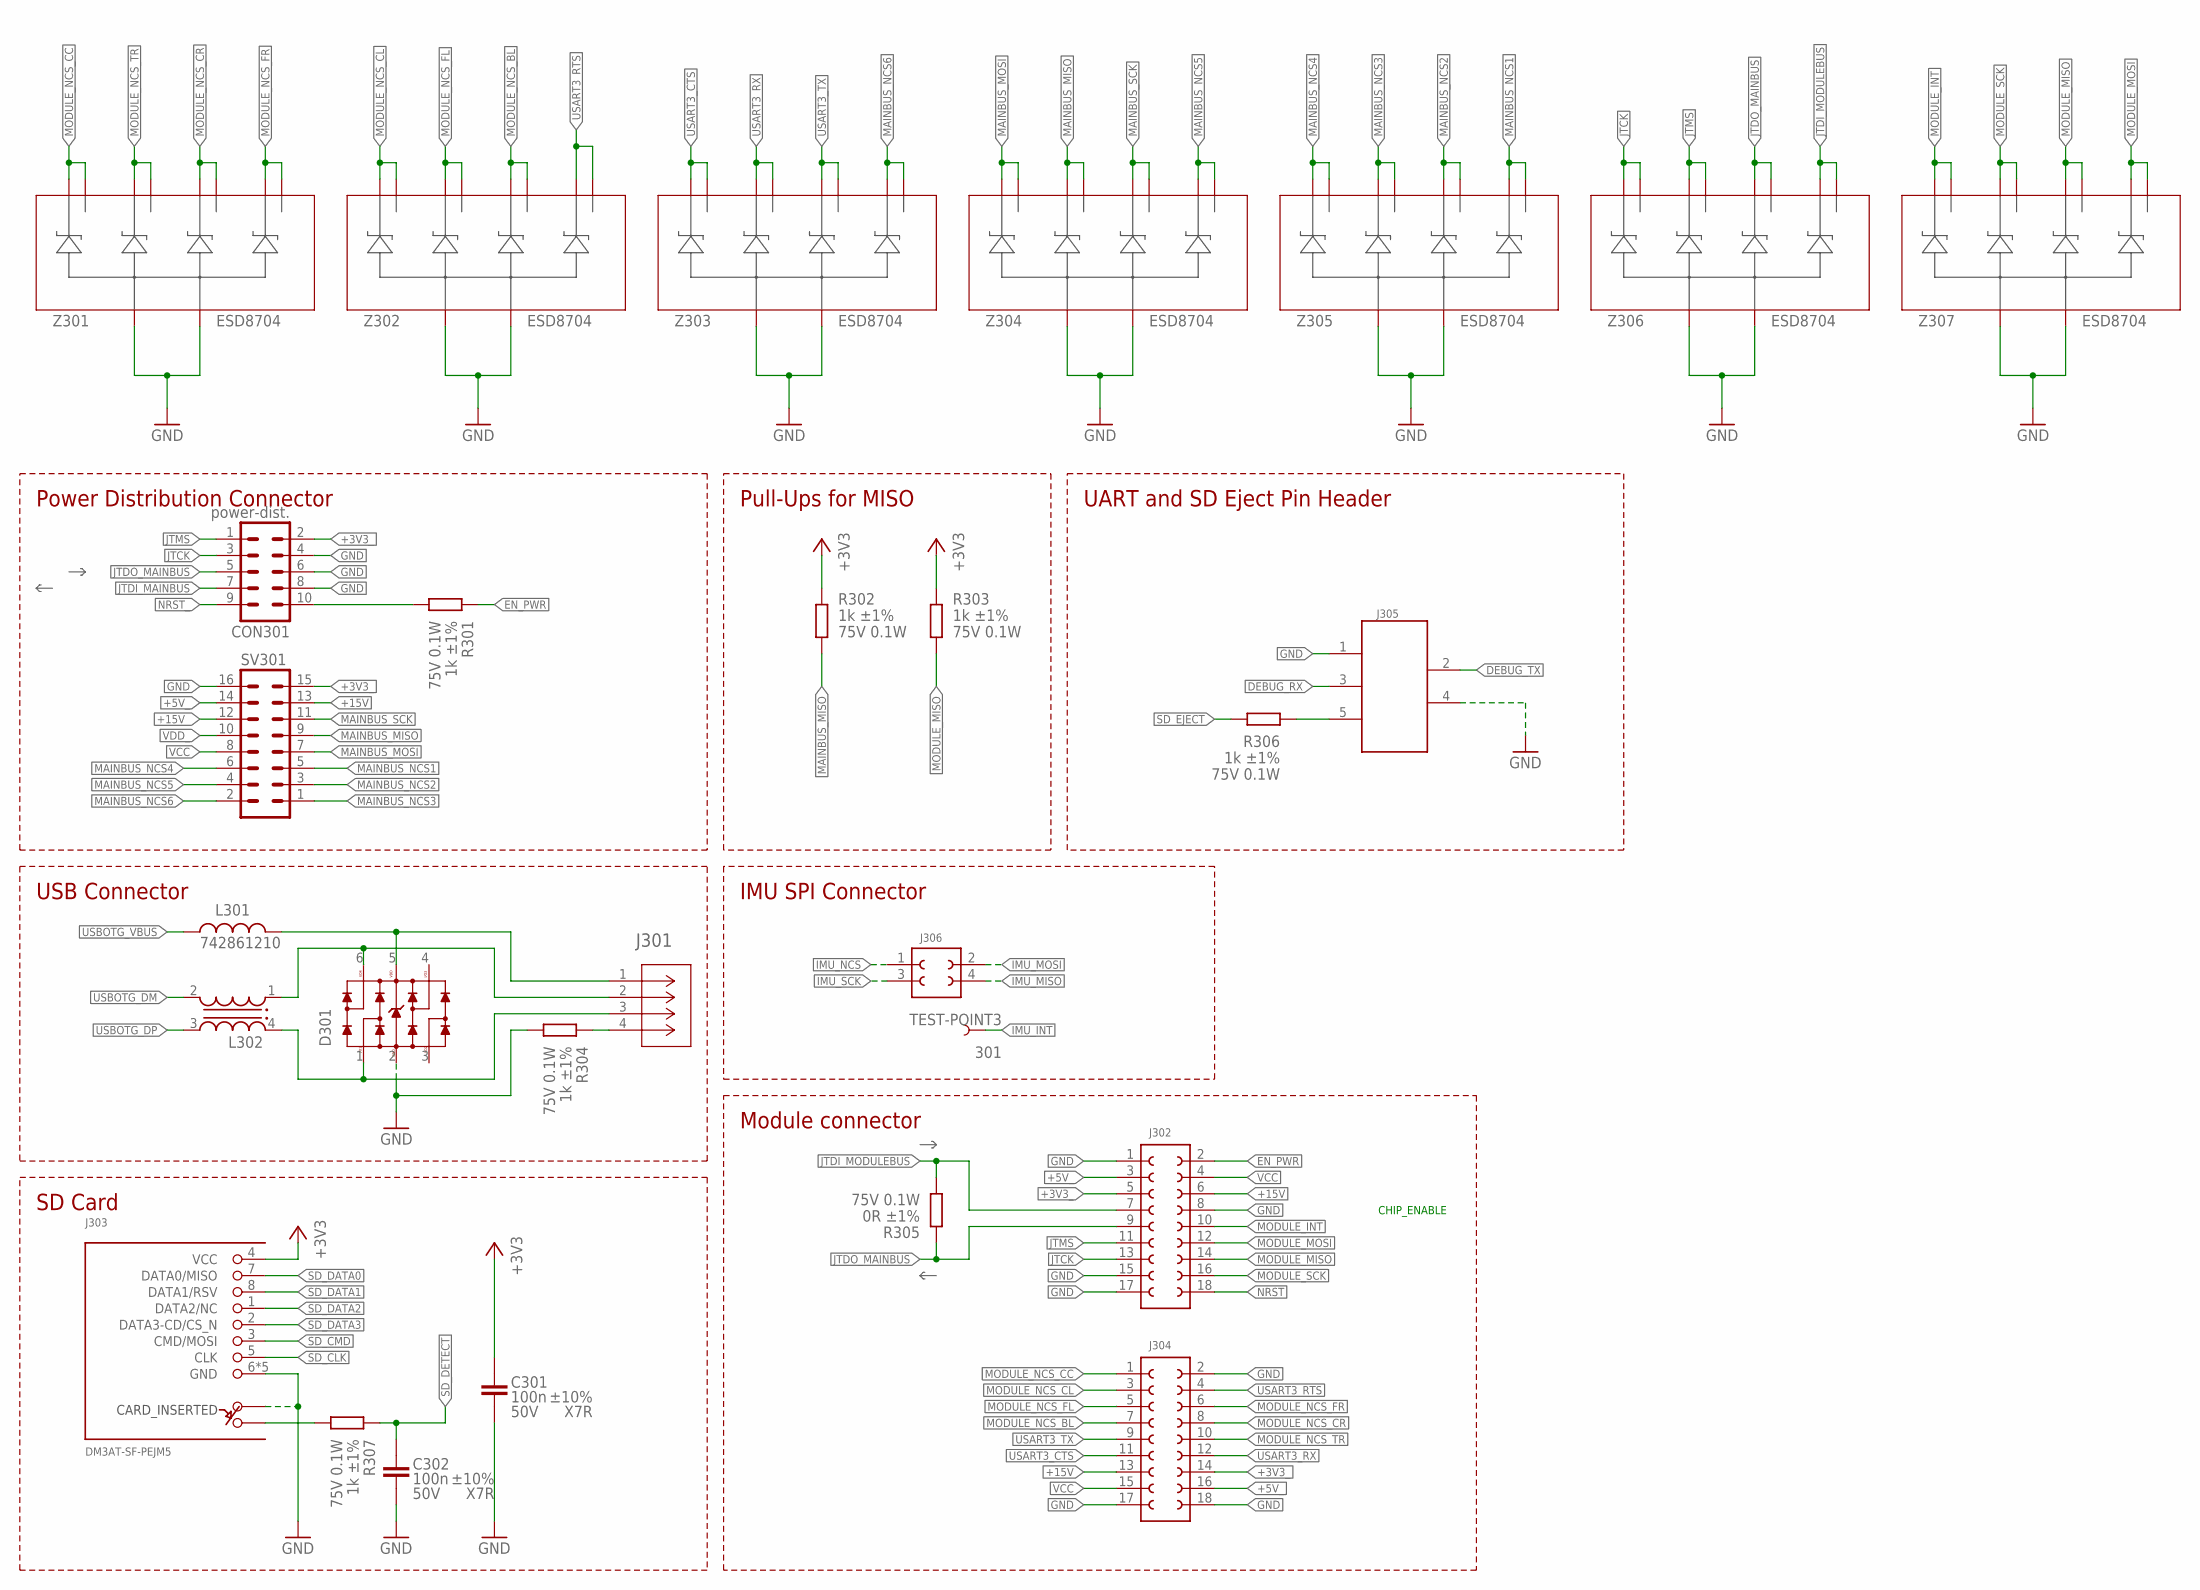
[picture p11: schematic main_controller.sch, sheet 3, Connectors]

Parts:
301: TEST-POINT3; PAD.03X.03
C301, C302: 100n ±10% 50V X7R; C0603
CON301: power-dist.; MA05-2; MPN 61301021121
D301: WE-TVS_824001; WE-TVS_SOT23-6L
J301: 530480410; CON_530480410_MOL
J302, J304: 610018243021; 610X1821821
J303: DM3AT-SF-PEJM5; MPN DM3AT-SF-PEJM5; MOUSER 798-DM3AT-SF-PEJM5
J305: 61000618221
J306: 623X0421021
L301: 742861210; WE-CBF_0603(W=2.6)
L302: WE-CNSW_1206_744232090; WE-CNSW_1206
R301, R302, R303, R304, R306, R307: 1k ±1% 75V 0.1W; R0603
R305: 0R ±1% 75V 0.1W; R0603
SV301: MA08-2
Z301, Z302, Z303, Z304, Z305, Z306, Z307: ESD8704; UDFN10

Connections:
+3V3: C301.1, J303.4 (VCC), R302.2, R303.2; also elsewhere on the board
+3V3_: CON301.2, J302.5 (3), J304.14 (12), SV301.15; also elsewhere on the board
+5V_: J302.3 (2), J304.16 (11), SV301.14; also elsewhere on the board
+15V: J302.6 (16), J304.13 (7), SV301.13
+15V_: SV301.12; also elsewhere on the board
DEBUG_RX: J305.3; also elsewhere on the board
DEBUG_TX: J305.2; also elsewhere on the board
EN_PWR: J302.2 (18), R301.2; also elsewhere on the board
GND: C301.2, C302.2, CON301.4, CON301.6, CON301.8, D301.2 (GND), J302.1, J302.8 (15), J302.15 (8), J302.17 (9), J303.6 (GND), J303.A, J303.MOUNT0 (GND), J303.MOUNT1 (GND), J303.MOUNT2 (GND), J303.MOUNT3 (GND), J304.2 (18), J304.17 (9), J304.18 (10), J305.1, J305.4, R304.1, SV301.16, Z301.3 (A), Z301.8 (A), Z302.3 (A), Z302.8 (A), Z303.3 (A), Z303.8 (A), Z304.3 (A), Z304.8 (A), Z305.3 (A), Z305.8 (A), Z306.3 (A), Z306.8 (A), Z307.3 (A), Z307.8 (A); also elsewhere on the board
IMU_INT: 301.P$1; also elsewhere on the board
IMU_MISO: J306.4 (3); also elsewhere on the board
IMU_MOSI: J306.2 (4); also elsewhere on the board
IMU_NCS: J306.1; also elsewhere on the board
IMU_SCK: J306.3 (2); also elsewhere on the board
JTCK: CON301.3, J302.13 (7), Z306.1 (C1), Z306.10 (D1); also elsewhere on the board
JTDI_MAINBUS: CON301.7; also elsewhere on the board
JTDI_MODULEBUS: J302.7 (4), R305.1, Z306.5 (C4), Z306.6 (D4); also elsewhere on the board
JTDO_MAINBUS: CON301.5, J302.9 (5), R305.2, Z306.4 (C3), Z306.7 (D3)
JTMS: CON301.1, J302.11 (6), Z306.2 (C2), Z306.9 (D2); also elsewhere on the board
MAINBUS_MISO: R302.1, SV301.9, Z304.2 (C2), Z304.9 (D2); also elsewhere on the board
MAINBUS_MOSI: SV301.7, Z304.1 (C1), Z304.10 (D1); also elsewhere on the board
MAINBUS_NCS1: SV301.5, Z305.5 (C4), Z305.6 (D4); also elsewhere on the board
MAINBUS_NCS2: SV301.3, Z305.4 (C3), Z305.7 (D3); also elsewhere on the board
MAINBUS_NCS3: SV301.1, Z305.2 (C2), Z305.9 (D2); also elsewhere on the board
MAINBUS_NCS4: SV301.6, Z305.1 (C1), Z305.10 (D1); also elsewhere on the board
MAINBUS_NCS5: SV301.4, Z304.5 (C4), Z304.6 (D4); also elsewhere on the board
MAINBUS_NCS6: SV301.2, Z303.5 (C4), Z303.6 (D4); also elsewhere on the board
MAINBUS_SCK: SV301.11, Z304.4 (C3), Z304.7 (D3); also elsewhere on the board
MODULE_INT: J302.10 (14), Z307.1 (C1), Z307.10 (D1); also elsewhere on the board
MODULE_MISO: J302.14 (12), R303.1, Z307.4 (C3), Z307.7 (D3); also elsewhere on the board
MODULE_MOSI: J302.12 (13), Z307.5 (C4), Z307.6 (D4); also elsewhere on the board
MODULE_NCS_BL: J304.7 (4), Z302.4 (C3), Z302.7 (D3); also elsewhere on the board
MODULE_NCS_CC: J304.1, Z301.1 (C1), Z301.10 (D1); also elsewhere on the board
MODULE_NCS_CL: J304.3 (2), Z302.1 (C1), Z302.10 (D1); also elsewhere on the board
MODULE_NCS_CR: J304.8 (15), Z301.4 (C3), Z301.7 (D3); also elsewhere on the board
MODULE_NCS_FL: J304.5 (3), Z302.2 (C2), Z302.9 (D2); also elsewhere on the board
MODULE_NCS_FR: J304.6 (16), Z301.5 (C4), Z301.6 (D4); also elsewhere on the board
MODULE_NCS_TR: J304.10 (14), Z301.2 (C2), Z301.9 (D2); also elsewhere on the board
MODULE_SCK: J302.16 (11), Z307.2 (C2), Z307.9 (D2); also elsewhere on the board
unnamed: CON301.10, R301.1
unnamed: D301.6, J301.2, L302.1 (4)
unnamed: J305.5, R306.1
unnamed: J301.4, R304.2
unnamed: D301.1, J301.3, L302.4 (1)
unnamed: D301.5 (VDD), J301.1, L301.2
NRST: J302.18 (10); also elsewhere on the board
NRST_: CON301.9; also elsewhere on the board
SD_CARD_DETECT_GND: J303.B, R307.1
SD_CLK: J303.5 (CLK); also elsewhere on the board
SD_CMD: J303.3 (CMD/MOSI); also elsewhere on the board
SD_DATA0: J303.7 (DATA0/MISO); also elsewhere on the board
SD_DATA1: J303.8 (DATA1/RSV); also elsewhere on the board
SD_DATA2: J303.1 (DATA2/NC); also elsewhere on the board
SD_DATA3: J303.2 (DATA3-CD/CS_N); also elsewhere on the board
SD_DETECT: C302.1, R307.2; also elsewhere on the board
SD_EJECT: R306.2; also elsewhere on the board
USART3_CTS: J304.11 (6), Z303.1 (C1), Z303.10 (D1); also elsewhere on the board
USART3_RTS: J304.4 (17), Z302.5 (C4), Z302.6 (D4); also elsewhere on the board
USART3_RX: J304.12 (13), Z303.2 (C2), Z303.9 (D2); also elsewhere on the board
USART3_TX: J304.9 (5), Z303.4 (C3), Z303.7 (D3); also elsewhere on the board
USBOTG_DM: L302.2 (3); also elsewhere on the board
USBOTG_DP: L302.3 (2); also elsewhere on the board
USBOTG_VBUS: L301.1; also elsewhere on the board
VCC: J302.4 (17), J304.15 (8), SV301.8
VDD_: SV301.10; also elsewhere on the board

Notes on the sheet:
SD Card
Power Distribution Connector
USB Connector
CHIP_ENABLE
Module connector
Pull-Ups for MISO
UART and SD Eject Pin Header
IMU SPI Connector

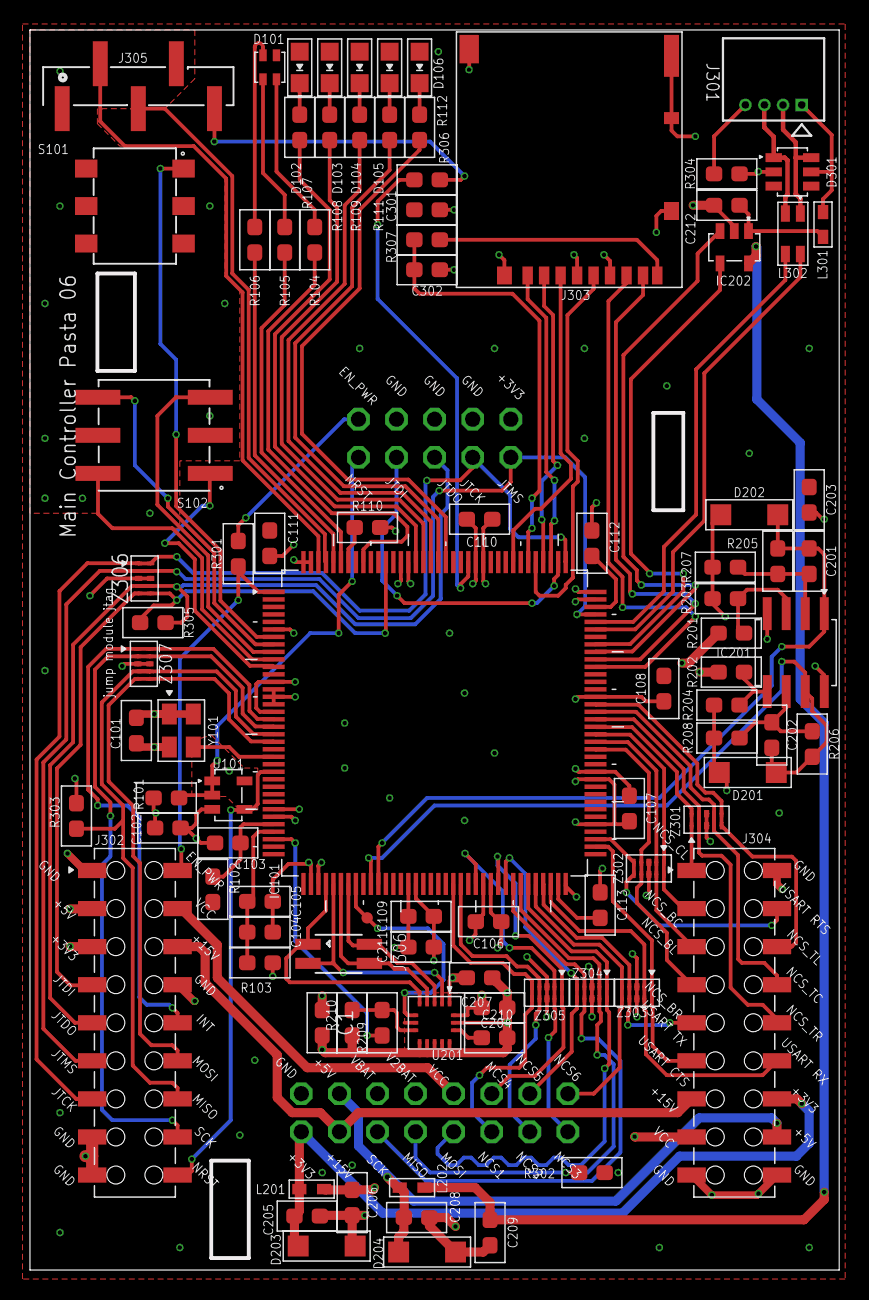
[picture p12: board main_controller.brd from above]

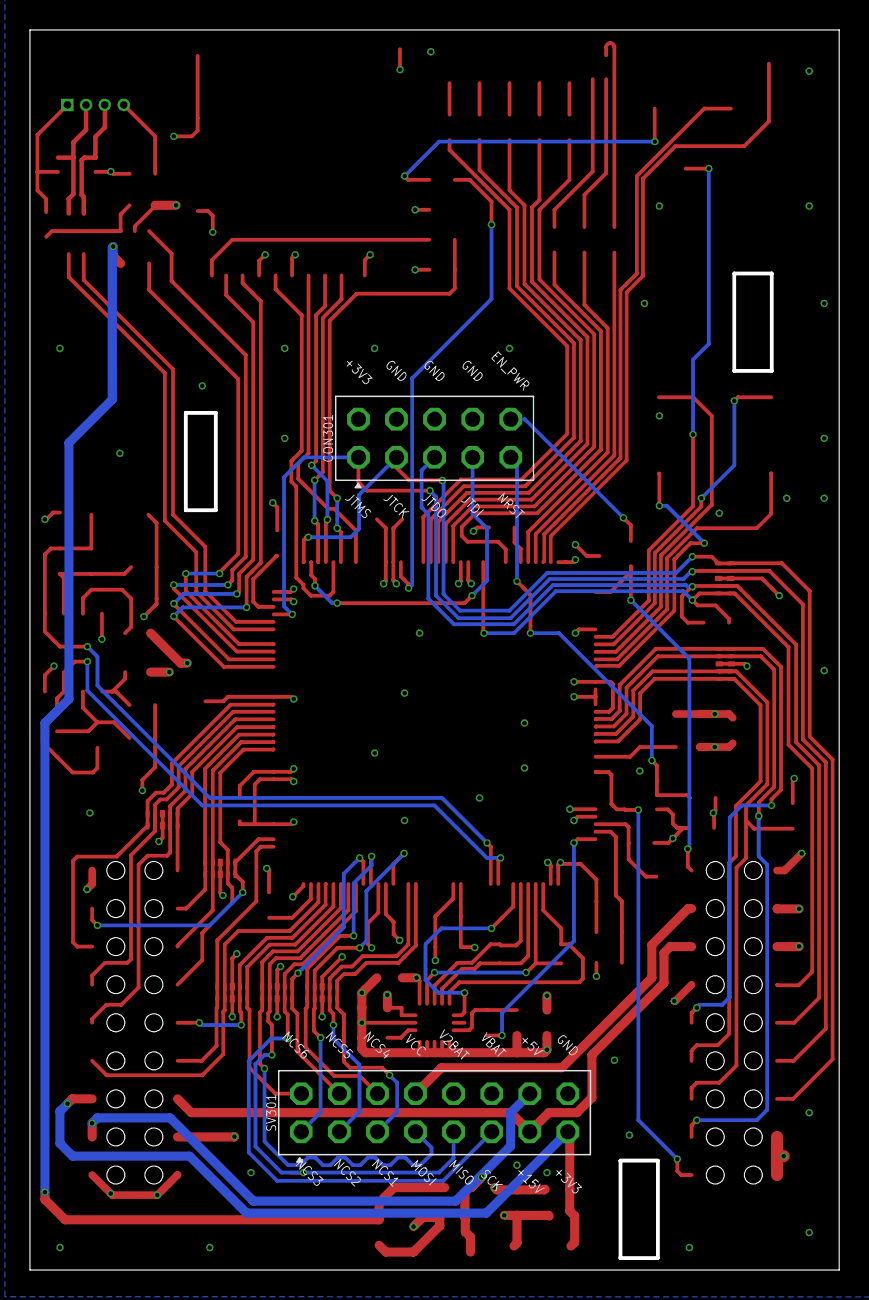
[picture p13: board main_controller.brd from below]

Board: 4 copper layers, 54.0 x 82.8 mm, 97 parts (2 on the bottom side), 104 nets.

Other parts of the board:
U$1: POWER_DISTRIBUTION_BOARD_TOP

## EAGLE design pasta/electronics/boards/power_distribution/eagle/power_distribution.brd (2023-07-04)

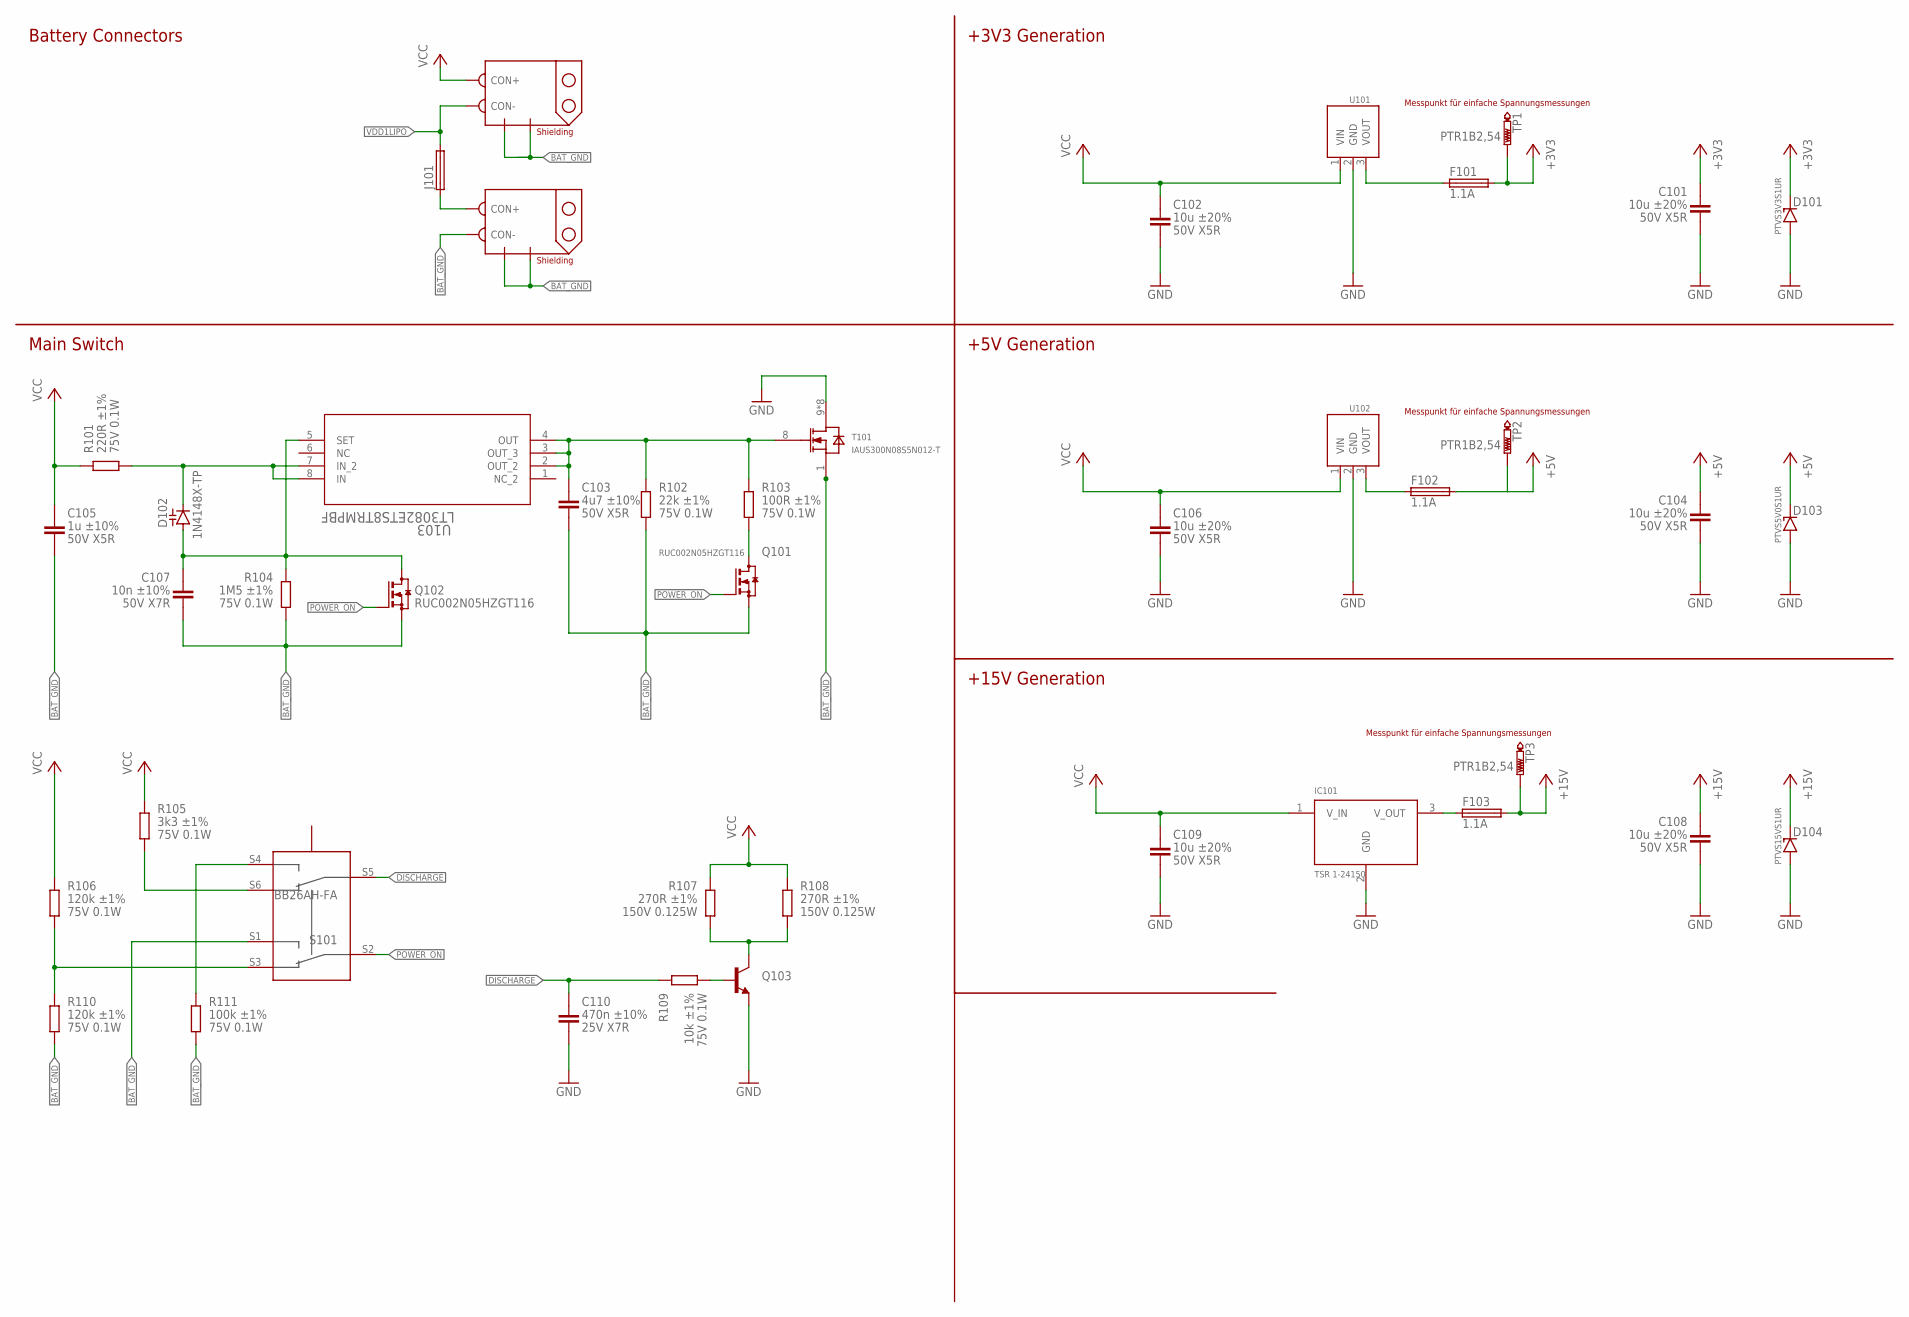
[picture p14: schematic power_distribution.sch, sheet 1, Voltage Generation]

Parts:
C101, C102, C104, C106, C108, C109: 10u ±20% 50V X5R; C1206
C103: 4u7 ±10% 50V X5R; C0805
C105: 1u ±10% 50V X5R; C0603
C107: 10n ±10% 50V X7R; C0603
C110: 470n ±10% 25V X7R; C0603
CON101, CON102: XT60PW; XT60PW-M
D101: PTVS3V3S1UR; SOD123
D102: 1N4148X-TP; SOD523
D103: PTVS5V0S1UR; SOD123
D104: PTVS15VS1UR; SOD123
F101, F102, F103: 1.1A; MF-NSMF-1
IC101: TSR 1-24150; TRACO_POWER_3_PIN
J101: 696107003002
Q101, Q102: RUC002N05HZGT116; SOT23
Q103: FJT44TF"; SOT223
R101: 220R ±1% 75V 0.1W; R0603
R102: 22k ±1% 75V 0.1W; R0603
R103: 100R ±1% 75V 0.1W; R0603
R104: 1M5 ±1% 75V 0.1W; R0603
R105: 3k3 ±1% 75V 0.1W; R0603
R106, R110: 120k ±1% 75V 0.1W; R0603
R107, R108: 270R ±1% 150V 0.125W; R0805
R109: 10k ±1% 75V 0.1W; R0603
R111: 100k ±1% 75V 0.1W; R0603
S101: BB26AH-FA; BB26AH
T101: IAUS300N08S5N012-T; SOIC120P1500X235-16N-1-V
TP1, TP2, TP3: PTR1B2,54; B2,54
U101: FDSM_SIP-3_173010342; FDSM-173XXXX42
U102: FDSM_SIP-3_173010542; FDSM-173XXXX42
U103: LT3082ETS8TRMPBF; TSOT-23_TS8

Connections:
+3V3: C101.1, D101.C (KATHODE), F101.2, TP1.TP; also elsewhere on the board
+5V: C104.1, D103.C (KATHODE), F102.2, TP2.TP; also elsewhere on the board
+15V: C108.1, D104.C (KATHODE), F103.2, TP3.TP; also elsewhere on the board
BAT_GND: C103.2, C105.2, C107.2, CON101.S1, CON101.S2, CON102.CON-, CON102.S1, CON102.S2, Q101.2 (S), Q102.2 (S), R102.1, R104.1, R110.1, R111.1, S101.S1 (2), T101.1 (SOURCE_1)
DISCHARGE: C110.1, R109.1, S101.S5 (4)
GND: C101.2, C102.2, C104.2, C106.2, C108.2, C109.2, C110.2, D101.A (ANODE), D103.A (ANODE), D104.A (ANODE), IC101.2 (GND), Q103.3 (E), T101.9 (DRAIN), T101.10 (DRAIN), T101.11 (DRAIN), T101.12 (DRAIN), T101.13 (DRAIN), T101.14 (DRAIN), T101.15 (DRAIN), T101.16 (DRAIN), U101.2 (GND), U102.2 (GND); also elsewhere on the board
unnamed: CON102.CON+, J101.1
unnamed: C103.1, R102.2, R103.2, T101.8 (GATE), U103.2 (OUT_2), U103.3 (OUT_3), U103.4 (OUT)
unnamed: Q101.3 (D), R103.1
unnamed: R106.1, R110.2, S101.S3 (3)
unnamed: F101.1, U101.3 (VOUT)
unnamed: R105.1, S101.S6 (6)
unnamed: F103.1, IC101.3 (V_OUT)
unnamed: R111.2, S101.S4 (5)
unnamed: F102.1, U102.3 (VOUT)
unnamed: Q103.2 (C), Q103.4 (C), R107.1, R108.1
unnamed: Q103.1 (B), R109.2
unnamed: D102.C, R101.1, U103.7 (IN_2), U103.8 (IN)
POWER_ON: Q101.1 (G), Q102.1 (G), S101.S2 (1)
SETPIN: C107.1, D102.A, Q102.3 (D), R104.2, U103.5 (SET)
VCC: C102.1, C105.1, C106.1, C109.1, CON101.CON+, IC101.1 (V_IN), R101.2, R105.2, R106.2, R107.2, R108.2, U101.1 (VIN), U102.1 (VIN); also elsewhere on the board
VDD1LIPO: CON101.CON-, J101.2; also elsewhere on the board

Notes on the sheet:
+3V3 Generation
+5V Generation
+15V Generation
Main Switch
Battery Connectors
Messpunkt für einfache Spannungsmessungen

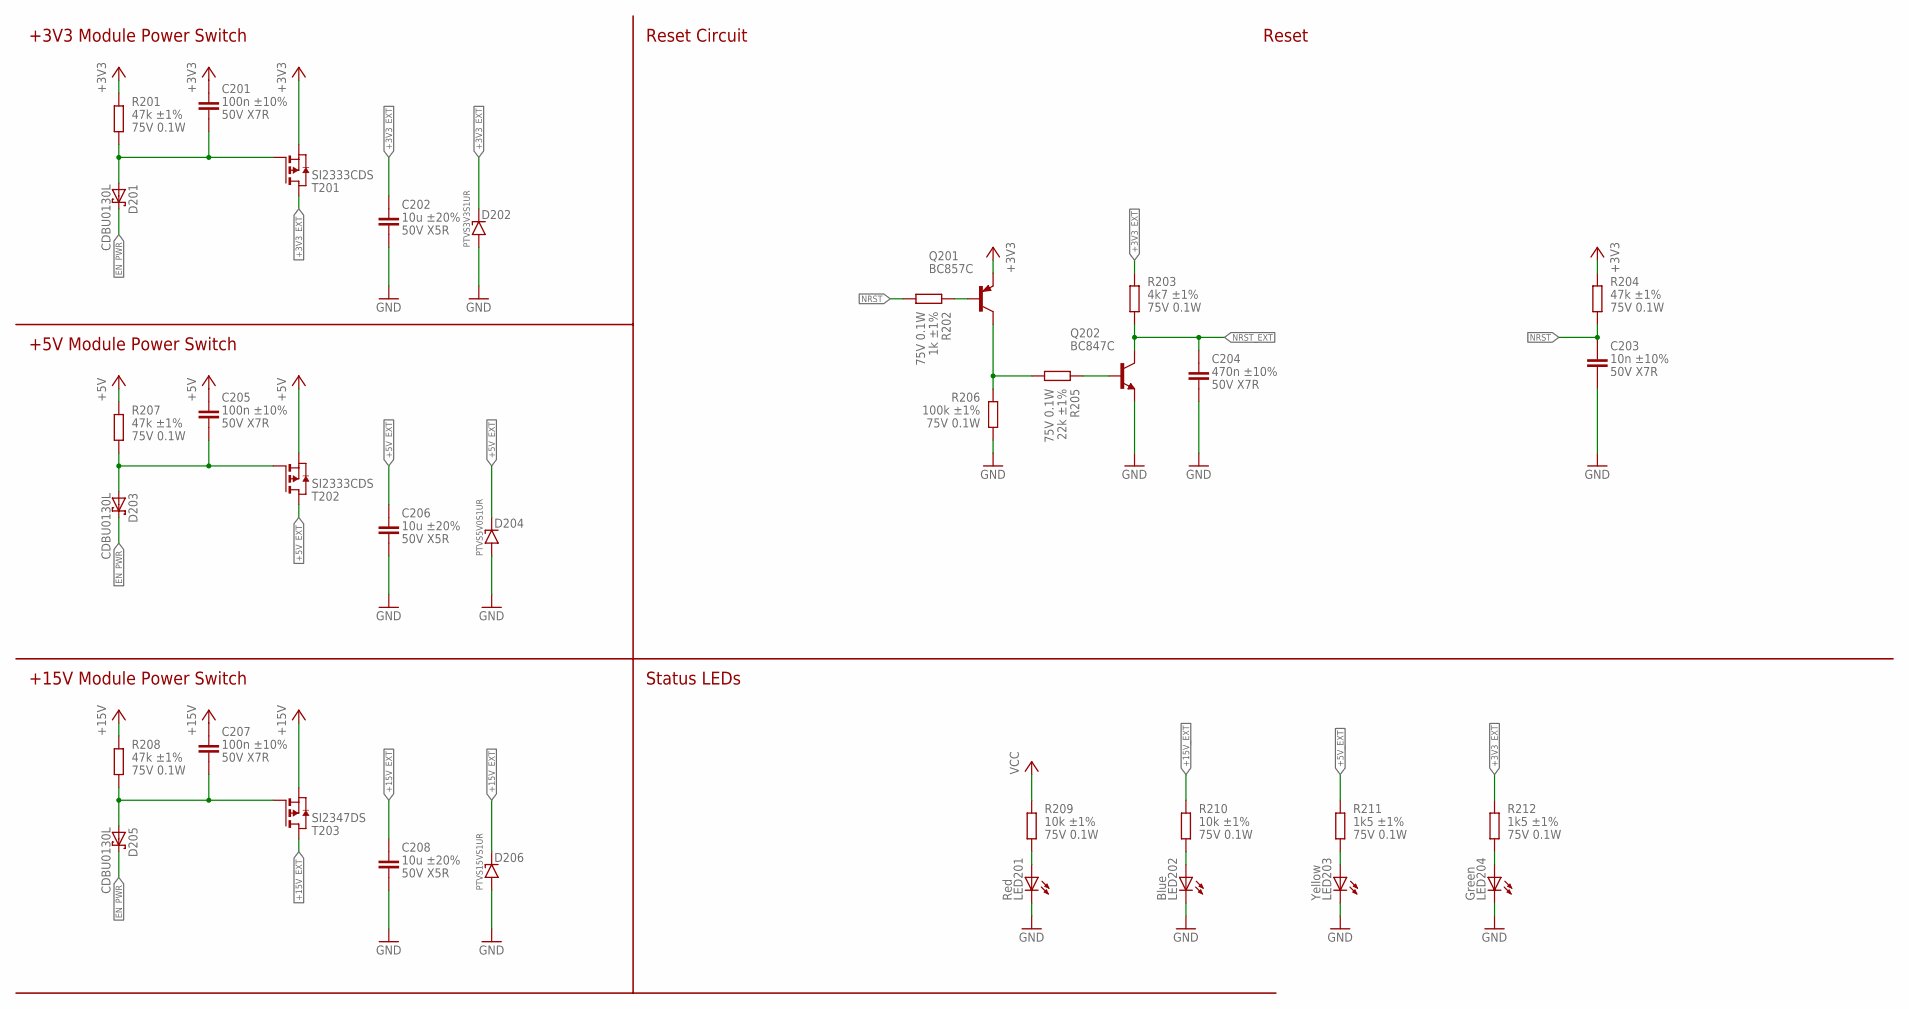
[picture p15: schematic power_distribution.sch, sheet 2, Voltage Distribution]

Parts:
C201, C205, C207: 100n ±10% 50V X7R; C0603
C202, C206, C208: 10u ±20% 50V X5R; C1206
C203: 10n ±10% 50V X7R; C0603
C204: 470n ±10% 50V X7R; C0603
D201, D203, D205: CDBU0130L; 0603
D202: PTVS3V3S1UR; SOD123
D204: PTVS5V0S1UR; SOD123
D206: PTVS15VS1UR; SOD123
LED201: Red; CHIPLED_0805
LED202: Blue; CHIPLED_0805
LED203: Yellow; CHIPLED_0805
LED204: Green; CHIPLED_0805
Q201: BC857C; SOT23-BEC; MPN BC857CW,115; MOUSER 771-BC857CW115
Q202: BC847C; SOT23; MPN BC847CW,115; MOUSER 771-BC847CW-T/R
R201, R204, R207, R208: 47k ±1% 75V 0.1W; R0603
R202: 1k ±1% 75V 0.1W; R0603
R203: 4k7 ±1% 75V 0.1W; R0603
R205: 22k ±1% 75V 0.1W; R0603
R206: 100k ±1% 75V 0.1W; R0603
R209, R210: 10k ±1% 75V 0.1W; R0603
R211, R212: 1k5 ±1% 75V 0.1W; R0603
T201, T202: SI2333CDS; SOT23
T203: SI2347DS; SOT23

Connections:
+3V3: C201.1, Q201.E, R201.2, R204.2, T201.2 (S); also elsewhere on the board
+3V3_EXT: C202.1, D202.C (KATHODE), R203.2, R212.2, T201.3 (D); also elsewhere on the board
+5V: C205.1, R207.2, T202.2 (S); also elsewhere on the board
+5V_EXT: C206.1, D204.C (KATHODE), R211.2, T202.3 (D); also elsewhere on the board
+15V: C207.1, R208.2, T203.2 (S); also elsewhere on the board
+15V_EXT: C208.1, D206.C (KATHODE), R210.2, T203.3 (D); also elsewhere on the board
EN_PWR: D201.2 (C), D203.2 (C), D205.2 (C); also elsewhere on the board
GND: C202.2, C203.2, C204.2, C206.2, C208.2, D202.A (ANODE), D204.A (ANODE), D206.A (ANODE), LED201.C, LED202.C, LED203.C, LED204.C, Q202.2 (E), R206.1; also elsewhere on the board
unnamed: LED201.A, R209.1
unnamed: C201.2, D201.1 (A), R201.1, T201.1 (G)
unnamed: C205.2, D203.1 (A), R207.1, T202.1 (G)
unnamed: C207.2, D205.1 (A), R208.1, T203.1 (G)
unnamed: LED204.A, R212.1
unnamed: LED203.A, R211.1
unnamed: Q201.B, R202.2
unnamed: Q201.C, R205.1, R206.2
unnamed: Q202.1 (B), R205.2
unnamed: LED202.A, R210.1
NRST: C203.1, R202.1, R204.1; also elsewhere on the board
NRST_EXT: C204.1, Q202.3 (C), R203.1; also elsewhere on the board
VCC: R209.2; also elsewhere on the board

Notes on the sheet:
+3V3 Module Power Switch
+5V Module Power Switch
+15V Module Power Switch
Status LEDs
Reset Circuit
Reset

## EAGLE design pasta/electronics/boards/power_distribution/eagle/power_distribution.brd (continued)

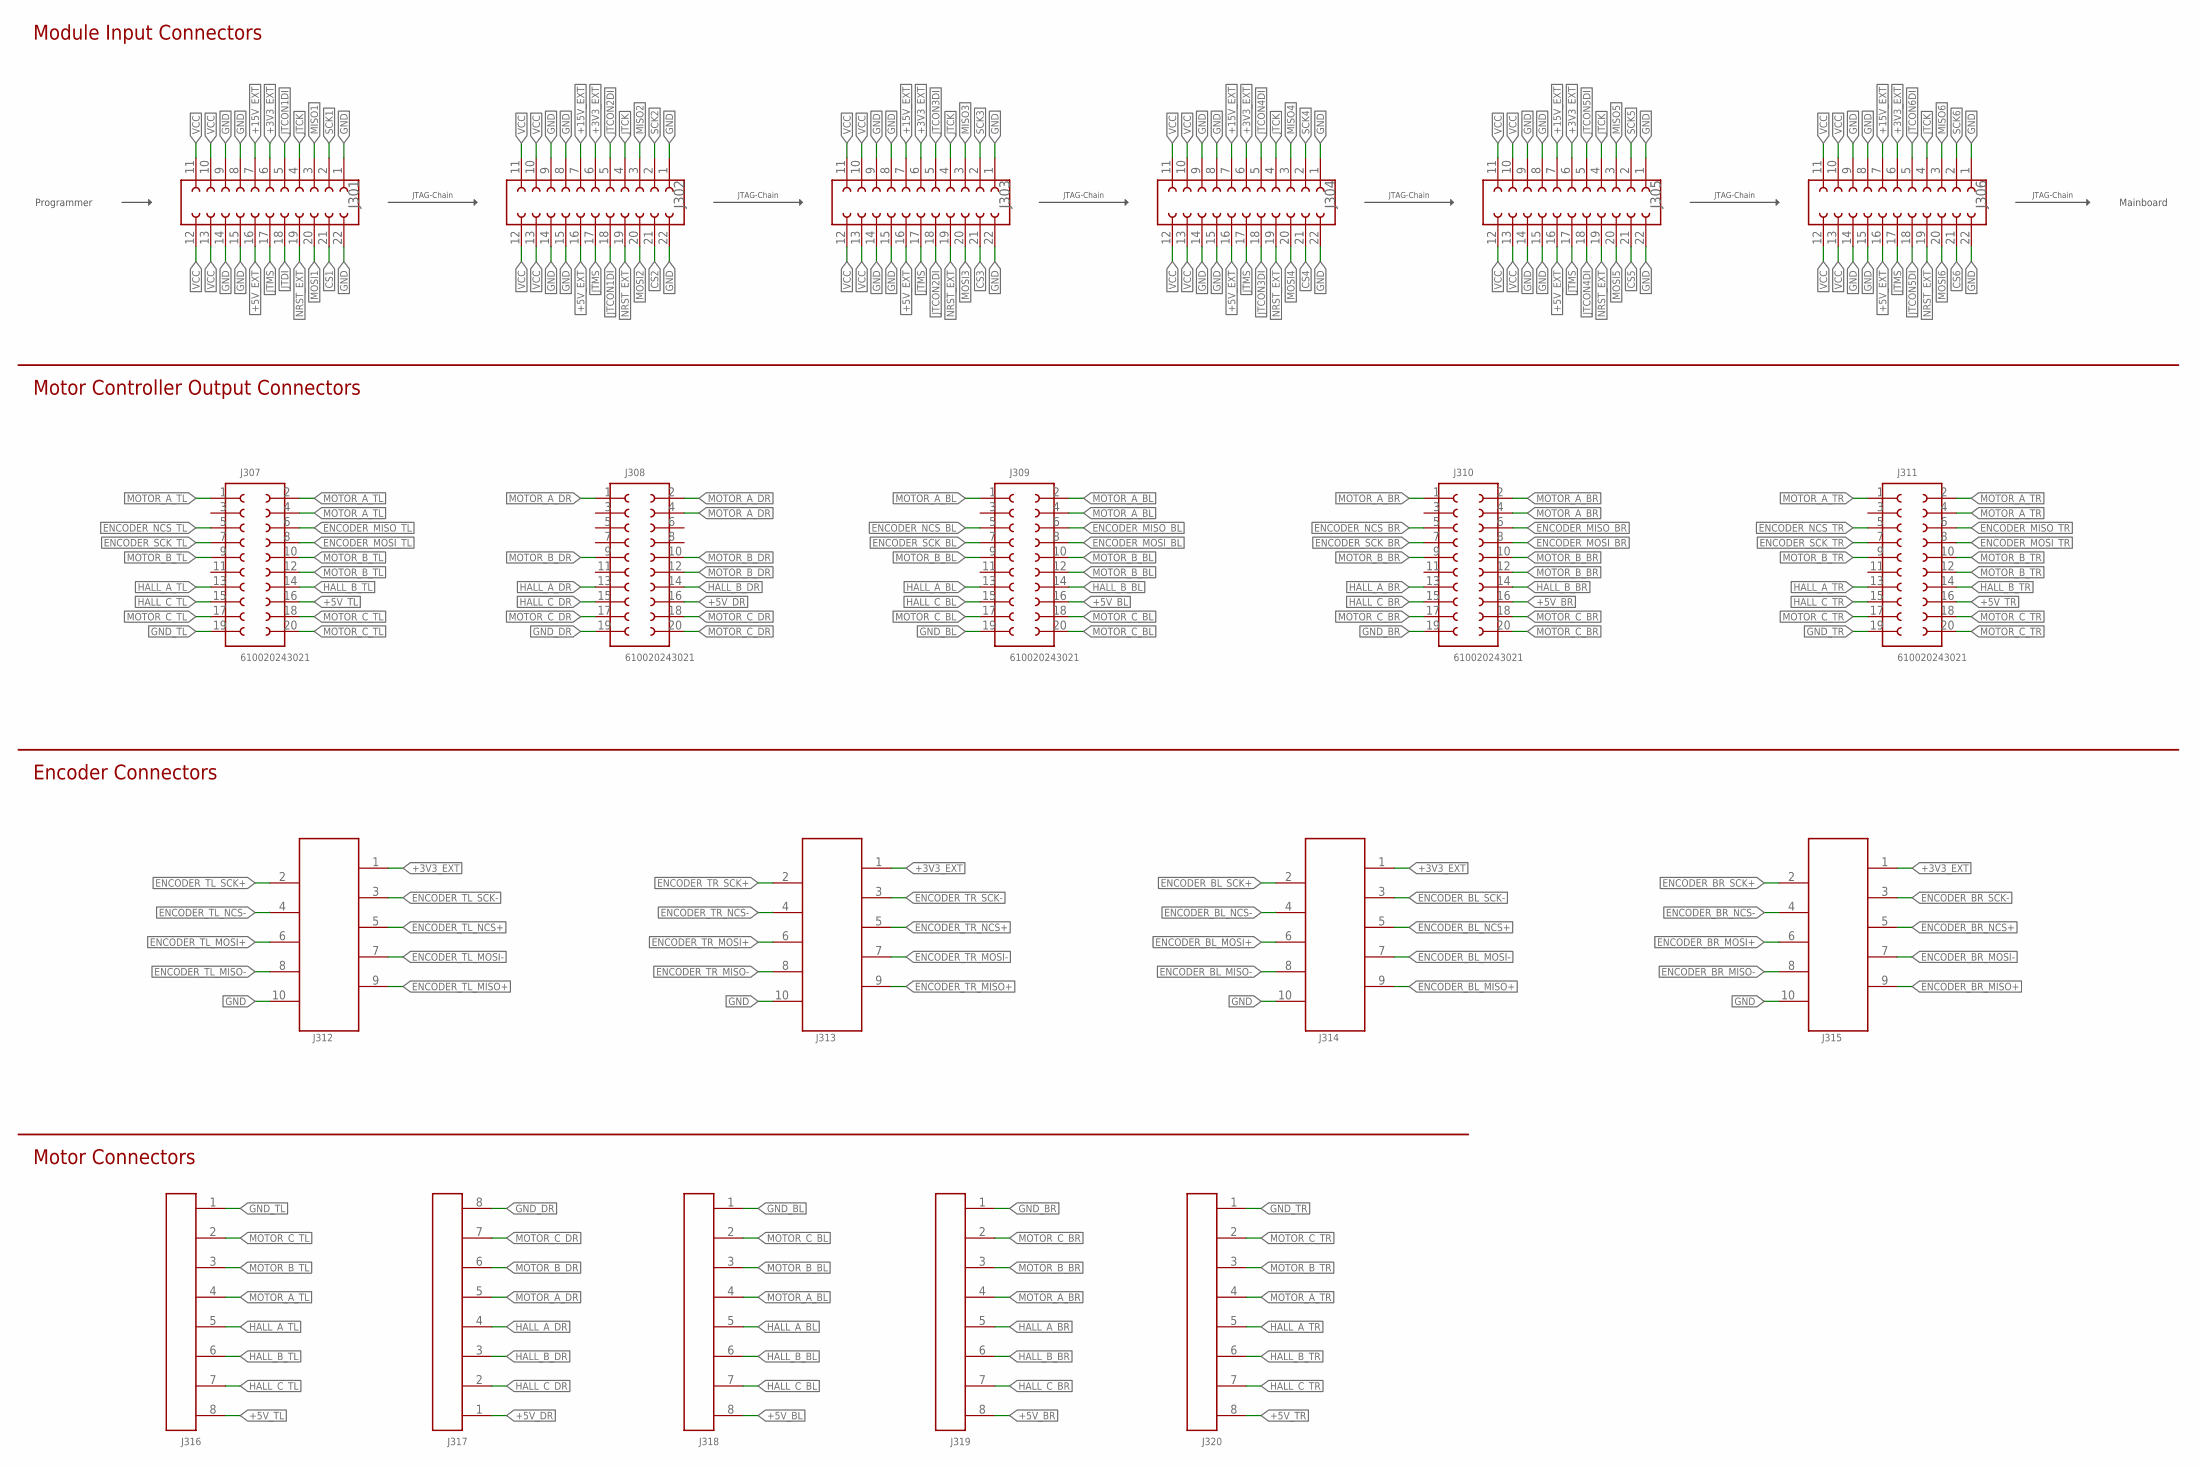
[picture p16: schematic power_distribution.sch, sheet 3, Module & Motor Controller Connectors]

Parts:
J301, J302, J303, J304, J305, J306: 610022243021
J307, J308, J309, J310, J311: 610020243021; 610X20243021
J312, J313, J314, J315: 690368171072
J316, J318, J319, J320: 66100811622
J317: 66100811722

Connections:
+3V3_EXT: J301.6, J302.6, J303.6, J304.6, J305.6, J306.6, J312.1 (10), J313.1 (10), J314.1 (10), J315.1 (10); also elsewhere on the board
+5V_BL: J309.16 (8), J318.8
+5V_BR: J310.16 (8), J319.8
+5V_DR: J308.16 (8), J317.1 (8)
+5V_EXT: J301.16, J302.16, J303.16, J304.16, J305.16, J306.16; also elsewhere on the board
+5V_TL: J307.16 (8), J316.8
+5V_TR: J311.16 (8), J320.8
+15V_EXT: J301.7, J302.7, J303.7, J304.7, J305.7, J306.7; also elsewhere on the board
CS1: J301.21; also elsewhere on the board
CS2: J302.21; also elsewhere on the board
CS3: J303.21; also elsewhere on the board
CS4: J304.21; also elsewhere on the board
CS5: J305.21; also elsewhere on the board
CS6: J306.21; also elsewhere on the board
ENCODER_BL_MISO+: J314.9 (2); also elsewhere on the board
ENCODER_BL_MISO-: J314.8 (3); also elsewhere on the board
ENCODER_BL_MOSI+: J314.6 (5); also elsewhere on the board
ENCODER_BL_MOSI-: J314.7 (4); also elsewhere on the board
ENCODER_BL_NCS+: J314.5 (6); also elsewhere on the board
ENCODER_BL_NCS-: J314.4 (7); also elsewhere on the board
ENCODER_BL_SCK+: J314.2 (9); also elsewhere on the board
ENCODER_BL_SCK-: J314.3 (8); also elsewhere on the board
ENCODER_BR_MISO+: J315.9 (2); also elsewhere on the board
ENCODER_BR_MISO-: J315.8 (3); also elsewhere on the board
ENCODER_BR_MOSI+: J315.6 (5); also elsewhere on the board
ENCODER_BR_MOSI-: J315.7 (4); also elsewhere on the board
ENCODER_BR_NCS+: J315.5 (6); also elsewhere on the board
ENCODER_BR_NCS-: J315.4 (7); also elsewhere on the board
ENCODER_BR_SCK+: J315.2 (9); also elsewhere on the board
ENCODER_BR_SCK-: J315.3 (8); also elsewhere on the board
ENCODER_MISO_BL: J309.6 (3); also elsewhere on the board
ENCODER_MISO_BR: J310.6 (3); also elsewhere on the board
ENCODER_MISO_TL: J307.6 (3); also elsewhere on the board
ENCODER_MISO_TR: J311.6 (3); also elsewhere on the board
ENCODER_MOSI_BL: J309.8 (4); also elsewhere on the board
ENCODER_MOSI_BR: J310.8 (4); also elsewhere on the board
ENCODER_MOSI_TL: J307.8 (4); also elsewhere on the board
ENCODER_MOSI_TR: J311.8 (4); also elsewhere on the board
ENCODER_NCS_BL: J309.5 (18); also elsewhere on the board
ENCODER_NCS_BR: J310.5 (18); also elsewhere on the board
ENCODER_NCS_TL: J307.5 (18); also elsewhere on the board
ENCODER_NCS_TR: J311.5 (18); also elsewhere on the board
ENCODER_SCK_BL: J309.7 (17); also elsewhere on the board
ENCODER_SCK_BR: J310.7 (17); also elsewhere on the board
ENCODER_SCK_TL: J307.7 (17); also elsewhere on the board
ENCODER_SCK_TR: J311.7 (17); also elsewhere on the board
ENCODER_TL_MISO+: J312.9 (2); also elsewhere on the board
ENCODER_TL_MISO-: J312.8 (3); also elsewhere on the board
ENCODER_TL_MOSI+: J312.6 (5); also elsewhere on the board
ENCODER_TL_MOSI-: J312.7 (4); also elsewhere on the board
ENCODER_TL_NCS+: J312.5 (6); also elsewhere on the board
ENCODER_TL_NCS-: J312.4 (7); also elsewhere on the board
ENCODER_TL_SCK+: J312.2 (9); also elsewhere on the board
ENCODER_TL_SCK-: J312.3 (8); also elsewhere on the board
ENCODER_TR_MISO+: J313.9 (2); also elsewhere on the board
ENCODER_TR_MISO-: J313.8 (3); also elsewhere on the board
ENCODER_TR_MOSI+: J313.6 (5); also elsewhere on the board
ENCODER_TR_MOSI-: J313.7 (4); also elsewhere on the board
ENCODER_TR_NCS+: J313.5 (6); also elsewhere on the board
ENCODER_TR_NCS-: J313.4 (7); also elsewhere on the board
ENCODER_TR_SCK+: J313.2 (9); also elsewhere on the board
ENCODER_TR_SCK-: J313.3 (8); also elsewhere on the board
GND: J301.1, J301.8, J301.9, J301.14, J301.15, J301.22, J302.1, J302.8, J302.9, J302.14, J302.15, J302.22, J303.1, J303.8, J303.9, J303.14, J303.15, J303.22, J304.1, J304.8, J304.9, J304.14, J304.15, J304.22, J305.1, J305.8, J305.9, J305.14, J305.15, J305.22, J306.1, J306.8, J306.9, J306.14, J306.15, J306.22, J312.10 (1), J313.10 (1), J314.10 (1), J315.10 (1); also elsewhere on the board
GND_BL: J309.19 (11), J318.1
GND_BR: J310.19 (11), J319.1
GND_DR: J308.19 (11), J317.8 (1)
GND_TL: J307.19 (11), J316.1
GND_TR: J311.19 (11), J320.1
HALL_A_BL: J309.13 (14), J318.5
HALL_A_BR: J310.13 (14), J319.5
HALL_A_DR: J308.13 (14), J317.4 (5)
HALL_A_TL: J307.13 (14), J316.5
HALL_A_TR: J311.13 (14), J320.5
HALL_B_BL: J309.14 (7), J318.6
HALL_B_BR: J310.14 (7), J319.6
HALL_B_DR: J308.14 (7), J317.3 (6)
HALL_B_TL: J307.14 (7), J316.6
HALL_B_TR: J311.14 (7), J320.6
HALL_C_BL: J309.15 (13), J318.7
HALL_C_BR: J310.15 (13), J319.7
HALL_C_DR: J308.15 (13), J317.2 (7)
HALL_C_TL: J307.15 (13), J316.7
HALL_C_TR: J311.15 (13), J320.7
JTCK: J301.4, J302.4, J303.4, J304.4, J305.4, J306.4; also elsewhere on the board
JTCON1DI: J301.5, J302.18; also elsewhere on the board
JTCON2DI: J302.5, J303.18; also elsewhere on the board
JTCON3DI: J303.5, J304.18; also elsewhere on the board
JTCON4DI: J304.5, J305.18; also elsewhere on the board
JTCON5DI: J305.5, J306.18; also elsewhere on the board
JTCON6DI: J306.5; also elsewhere on the board
JTDI: J301.18; also elsewhere on the board
JTMS: J301.17, J302.17, J303.17, J304.17, J305.17, J306.17; also elsewhere on the board
MISO1: J301.3; also elsewhere on the board
MISO2: J302.3; also elsewhere on the board
MISO3: J303.3; also elsewhere on the board
MISO4: J304.3; also elsewhere on the board
MISO5: J305.3; also elsewhere on the board
MISO6: J306.3; also elsewhere on the board
MOSI1: J301.20; also elsewhere on the board
MOSI2: J302.20; also elsewhere on the board
MOSI3: J303.20; also elsewhere on the board
MOSI4: J304.20; also elsewhere on the board
MOSI5: J305.20; also elsewhere on the board
MOSI6: J306.20; also elsewhere on the board
MOTOR_A_BL: J309.1 (20), J309.2 (1), J309.4 (2), J318.4
MOTOR_A_BR: J310.1 (20), J310.2 (1), J310.4 (2), J319.4
MOTOR_A_DR: J308.1 (20), J308.2 (1), J308.4 (2), J317.5 (4)
MOTOR_A_TL: J307.1 (20), J307.2 (1), J307.4 (2), J316.4
MOTOR_A_TR: J311.1 (20), J311.2 (1), J311.4 (2), J320.4
MOTOR_B_BL: J309.9 (16), J309.10 (5), J309.12 (6), J318.3
MOTOR_B_BR: J310.9 (16), J310.10 (5), J310.12 (6), J319.3
MOTOR_B_DR: J308.9 (16), J308.10 (5), J308.12 (6), J317.6 (3)
MOTOR_B_TL: J307.9 (16), J307.10 (5), J307.12 (6), J316.3
MOTOR_B_TR: J311.9 (16), J311.10 (5), J311.12 (6), J320.3
MOTOR_C_BL: J309.17 (12), J309.18 (9), J309.20 (10), J318.2
MOTOR_C_BR: J310.17 (12), J310.18 (9), J310.20 (10), J319.2
MOTOR_C_DR: J308.17 (12), J308.18 (9), J308.20 (10), J317.7 (2)
MOTOR_C_TL: J307.17 (12), J307.18 (9), J307.20 (10), J316.2
MOTOR_C_TR: J311.17 (12), J311.18 (9), J311.20 (10), J320.2
NRST_EXT: J301.19, J302.19, J303.19, J304.19, J305.19, J306.19; also elsewhere on the board
SCK1: J301.2; also elsewhere on the board
SCK2: J302.2; also elsewhere on the board
SCK3: J303.2; also elsewhere on the board
SCK4: J304.2; also elsewhere on the board
SCK5: J305.2; also elsewhere on the board
SCK6: J306.2; also elsewhere on the board
VCC: J301.10, J301.11, J301.12, J301.13, J302.10, J302.11, J302.12, J302.13, J303.10, J303.11, J303.12, J303.13, J304.10, J304.11, J304.12, J304.13, J305.10, J305.11, J305.12, J305.13, J306.10, J306.11, J306.12, J306.13; also elsewhere on the board

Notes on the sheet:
Module Input Connectors
JTAG-Chain
Mainboard
Programmer
Motor Controller Output Connectors
Encoder Connectors
Motor Connectors


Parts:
C401, C402, C403, C404, C408, C409: 100n ±10% 50V X7R; C0603
C405, C406, C407: 10u ±20% 50V X5R; C1206
D401, D402, D403, D404, D405, D406, D407, D408, D409, D410, D411: CDSOD323; SOD-323; MPN CDSOD323-T03C; MOUSER 652-CDSOD323-T03C
H401, H402, H403, H404: WA-SMSI_9774360; 9774***360
J401: 610016243021; 610X16243021
J402: 610010243021; 610X10243021
J403: 690367181672
J404: 61018243021; 610X18243021
JP401: JP1E; JP1
R401, R402, R405, R406, R407, R408: 10k ±1% 75V 0.1W; R0603
R403: 4k7 ±1% 75V 0.1W; R0603
R404: 1k ±1% 75V 0.1W; R0603
TP4, TP5, TP6, TP7: PTR1B2,54; B2,54
X401: CORESIGHT-JTAG-10THD10R; ML10R; MPN 61201021721
X402: RX; 3POL254
X403: TX; 2POL254

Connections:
15V_MEAS: C401.1, J401.5 (3), R401.1
30V_MEAS: C402.1, J401.7 (4), R402.1
!FB_DISCHARGE: C404.2, J404.7 (4), R406.1
+3V3: J401.2 (16), J402.2 (10); also elsewhere on the board
+3V3_EXT: C405.1, TP4.TP, X401.1 (VREF); also elsewhere on the board
+5V: J401.3 (2); also elsewhere on the board
+5V_EXT: TP5.TP; also elsewhere on the board
+15V: J401.4 (15); also elsewhere on the board
+15V_EXT: C406.1, C407.1, TP6.TP, X402.1, X403.1; also elsewhere on the board
CS1PDB: J401.12 (11); also elsewhere on the board
CS2PDB: J401.14 (10); also elsewhere on the board
CS3PDB: J401.16 (9); also elsewhere on the board
CS4PDB: J401.11 (6); also elsewhere on the board
CS5PDB: J401.13 (7); also elsewhere on the board
CS6PDB: J401.15 (8); also elsewhere on the board
EN_PWR: R403.1, R404.1; also elsewhere on the board
FB_CHARGE: C408.1, J404.9 (5), R407.2
FB_GND: J403.3 (14), J403.4 (13), J403.13 (4), J403.14 (3), J404.11 (6), J404.12 (13), J404.13 (7), J404.14 (12)
FB_KICK_CHIP: C403.1, J404.5 (3), R405.1
FB_KICK_LINEAR: C409.1, J404.6 (16), R408.1
FB_LIGHTBEAM: J404.8 (15), X402.2
FB_VCC: J403.1 (16), J403.2 (15), J403.15 (2), J403.16 (1), J404.15 (8), J404.16 (11), J404.17 (9), J404.18 (10)
FB_VOLTAGE_DATA+: J403.10 (7), J404.1
FB_VOLTAGE_DATA-: J403.7 (10), J404.2 (18)
FB_VOLTAGE_SCK+: J403.8 (9), J404.3 (2)
FB_VOLTAGE_SCK-: J403.9 (8), J404.4 (17)
GND: C401.2, C402.2, C403.2, C404.1, C405.2, C406.2, C407.2, C408.2, C409.2, D401.2 (ANODE), D402.2 (ANODE), D403.2 (ANODE), D404.2 (ANODE), D405.2 (ANODE), D406.2 (ANODE), D407.2 (ANODE), D408.2 (ANODE), D409.2 (ANODE), D410.2 (ANODE), D411.2 (ANODE), J401.1, J402.4 (9), J402.6 (8), J402.8 (7), JP401.1, TP7.TP, X401.3 (GND1), X401.5 (GND2), X402.3, X403.2; also elsewhere on the board
JTCK: D411.1 (KATHODE), J402.3 (2), X401.4 (TCK); also elsewhere on the board
JTCON1DI: D402.1 (KATHODE); also elsewhere on the board
JTCON2DI: D403.1 (KATHODE); also elsewhere on the board
JTCON3DI: D404.1 (KATHODE); also elsewhere on the board
JTCON4DI: D405.1 (KATHODE); also elsewhere on the board
JTCON5DI: D406.1 (KATHODE); also elsewhere on the board
JTCON6DI: D407.1 (KATHODE), J402.7 (4); also elsewhere on the board
JTDI: D401.1 (KATHODE), X401.8 (TDI); also elsewhere on the board
JTMAINDI: D408.1 (KATHODE), J402.5 (3), X401.6 (TDO)
JTMS: D410.1 (KATHODE), J402.1, X401.2 (TMS); also elsewhere on the board
JUMP_PWR: JP401.2, R404.2, X401.9 (HOTPLUG)
MISO: J401.8 (13); also elsewhere on the board
MOSI: J401.10 (12); also elsewhere on the board
unnamed: J403.5 (12), R407.1
unnamed: J403.6 (11), R405.2
unnamed: J402.10 (6), R403.2
unnamed: J403.11 (6), R408.2
unnamed: J403.12 (5), R406.2
NRST: D409.1 (KATHODE), J402.9 (5), X401.10 (SRST); also elsewhere on the board
SCK: J401.6 (14); also elsewhere on the board
VCC: J401.9 (5), R402.2; also elsewhere on the board
VDD1LIPO: R401.2; also elsewhere on the board

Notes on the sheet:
JTAG Connector
Mainboard Connector
JTAG TVS Diodes
Voltage Measurement Copper Pads
Spacers to POM Plate
JTAG Bridge for debugging purposes
Kicker Connectors
Connection to ball detection


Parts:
C501, C502: 330 µF; WCAP-AS5H_10X10.5(DXL)
RN501, RN502, RN503, RN504, RN505, RN506: 33R ±5% 50V 0.0625W; EXB38

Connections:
CS1: RN501.1-2 (2); also elsewhere on the board
CS1PDB: RN501.1-1 (1); also elsewhere on the board
CS2: RN502.1-2 (2); also elsewhere on the board
CS2PDB: RN502.1-1 (1); also elsewhere on the board
CS3: RN503.1-2 (2); also elsewhere on the board
CS3PDB: RN503.1-1 (1); also elsewhere on the board
CS4: RN504.1-2 (2); also elsewhere on the board
CS4PDB: RN504.1-1 (1); also elsewhere on the board
CS5: RN505.1-2 (2); also elsewhere on the board
CS5PDB: RN505.1-1 (1); also elsewhere on the board
CS6: RN506.1-2 (2); also elsewhere on the board
CS6PDB: RN506.1-1 (1); also elsewhere on the board
GND: C501.2 (-), C502.2 (-); also elsewhere on the board
MISO: RN501.3-1 (1), RN502.3-1 (1), RN503.3-1 (1), RN504.3-1 (1), RN505.3-1 (1), RN506.3-1 (1); also elsewhere on the board
MISO1: RN501.3-2 (2); also elsewhere on the board
MISO2: RN502.3-2 (2); also elsewhere on the board
MISO3: RN503.3-2 (2); also elsewhere on the board
MISO4: RN504.3-2 (2); also elsewhere on the board
MISO5: RN505.3-2 (2); also elsewhere on the board
MISO6: RN506.3-2 (2); also elsewhere on the board
MOSI: RN501.4-1 (1), RN502.4-1 (1), RN503.4-1 (1), RN504.4-1 (1), RN505.4-1 (1), RN506.4-1 (1); also elsewhere on the board
MOSI1: RN501.4-2 (2); also elsewhere on the board
MOSI2: RN502.4-2 (2); also elsewhere on the board
MOSI3: RN503.4-2 (2); also elsewhere on the board
MOSI4: RN504.4-2 (2); also elsewhere on the board
MOSI5: RN505.4-2 (2); also elsewhere on the board
MOSI6: RN506.4-2 (2); also elsewhere on the board
SCK: RN501.2-1 (1), RN502.2-1 (1), RN503.2-1 (1), RN504.2-1 (1), RN505.2-1 (1), RN506.2-1 (1); also elsewhere on the board
SCK1: RN501.2-2 (2); also elsewhere on the board
SCK2: RN502.2-2 (2); also elsewhere on the board
SCK3: RN503.2-2 (2); also elsewhere on the board
SCK4: RN504.2-2 (2); also elsewhere on the board
SCK5: RN505.2-2 (2); also elsewhere on the board
SCK6: RN506.2-2 (2); also elsewhere on the board
VCC: C501.1 (+), C502.1 (+); also elsewhere on the board

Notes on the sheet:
EMI Components
VCC Damping


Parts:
C601, C602, C603, C604, C605, C606, C607, C608: 100n ±10% 50V X7R; C0603
IC601, IC602, IC605, IC606: SN65LVDS050D; SO16
IC603, IC604, IC607, IC608: LVDS-DRIVER-DS90LV011AQ; SOT23-5
R601, R602, R603, R604: 100R ±1% 75V 0.1W; R0603

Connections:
+3V3_EXT: C601.1, C602.1, C603.1, C604.1, C605.1, C606.1, C607.1, C608.1, IC601.12 (DE), IC601.16 (VCC), IC602.12 (DE), IC602.16 (VCC), IC603.1 (VCC), IC604.1 (VCC), IC605.12 (DE), IC605.16 (VCC), IC606.12 (DE), IC606.16 (VCC), IC607.1 (VCC), IC608.1 (VCC); also elsewhere on the board
ENCODER_BL_MISO+: IC605.6 (2A), R603.2; also elsewhere on the board
ENCODER_BL_MISO-: IC605.7 (2B), R603.1; also elsewhere on the board
ENCODER_BL_MOSI+: IC607.4 (DOUT+); also elsewhere on the board
ENCODER_BL_MOSI-: IC607.3 (DOUT-); also elsewhere on the board
ENCODER_BL_NCS+: IC605.10 (2Y); also elsewhere on the board
ENCODER_BL_NCS-: IC605.11 (2Z); also elsewhere on the board
ENCODER_BL_SCK+: IC605.14 (1Y); also elsewhere on the board
ENCODER_BL_SCK-: IC605.13 (1Z); also elsewhere on the board
ENCODER_BR_MISO+: IC606.6 (2A), R604.2; also elsewhere on the board
ENCODER_BR_MISO-: IC606.7 (2B), R604.1; also elsewhere on the board
ENCODER_BR_MOSI+: IC608.4 (DOUT+); also elsewhere on the board
ENCODER_BR_MOSI-: IC608.3 (DOUT-); also elsewhere on the board
ENCODER_BR_NCS+: IC606.10 (2Y); also elsewhere on the board
ENCODER_BR_NCS-: IC606.11 (2Z); also elsewhere on the board
ENCODER_BR_SCK+: IC606.14 (1Y); also elsewhere on the board
ENCODER_BR_SCK-: IC606.13 (1Z); also elsewhere on the board
ENCODER_MISO_BL: IC605.5 (2R); also elsewhere on the board
ENCODER_MISO_BR: IC606.5 (2R); also elsewhere on the board
ENCODER_MISO_TL: IC601.5 (2R); also elsewhere on the board
ENCODER_MISO_TR: IC602.5 (2R); also elsewhere on the board
ENCODER_MOSI_BL: IC607.5 (DI); also elsewhere on the board
ENCODER_MOSI_BR: IC608.5 (DI); also elsewhere on the board
ENCODER_MOSI_TL: IC603.5 (DI); also elsewhere on the board
ENCODER_MOSI_TR: IC604.5 (DI); also elsewhere on the board
ENCODER_NCS_BL: IC605.4 (RE), IC605.9 (2D); also elsewhere on the board
ENCODER_NCS_BR: IC606.4 (RE), IC606.9 (2D); also elsewhere on the board
ENCODER_NCS_TL: IC601.4 (RE), IC601.9 (2D); also elsewhere on the board
ENCODER_NCS_TR: IC602.4 (RE), IC602.9 (2D); also elsewhere on the board
ENCODER_SCK_BL: IC605.15 (1D); also elsewhere on the board
ENCODER_SCK_BR: IC606.15 (1D); also elsewhere on the board
ENCODER_SCK_TL: IC601.15 (1D); also elsewhere on the board
ENCODER_SCK_TR: IC602.15 (1D); also elsewhere on the board
ENCODER_TL_MISO+: IC601.6 (2A), R601.2; also elsewhere on the board
ENCODER_TL_MISO-: IC601.7 (2B), R601.1; also elsewhere on the board
ENCODER_TL_MOSI+: IC603.4 (DOUT+); also elsewhere on the board
ENCODER_TL_MOSI-: IC603.3 (DOUT-); also elsewhere on the board
ENCODER_TL_NCS+: IC601.10 (2Y); also elsewhere on the board
ENCODER_TL_NCS-: IC601.11 (2Z); also elsewhere on the board
ENCODER_TL_SCK+: IC601.14 (1Y); also elsewhere on the board
ENCODER_TL_SCK-: IC601.13 (1Z); also elsewhere on the board
ENCODER_TR_MISO+: IC602.6 (2A), R602.2; also elsewhere on the board
ENCODER_TR_MISO-: IC602.7 (2B), R602.1; also elsewhere on the board
ENCODER_TR_MOSI+: IC604.4 (DOUT+); also elsewhere on the board
ENCODER_TR_MOSI-: IC604.3 (DOUT-); also elsewhere on the board
ENCODER_TR_NCS+: IC602.10 (2Y); also elsewhere on the board
ENCODER_TR_NCS-: IC602.11 (2Z); also elsewhere on the board
ENCODER_TR_SCK+: IC602.14 (1Y); also elsewhere on the board
ENCODER_TR_SCK-: IC602.13 (1Z); also elsewhere on the board
GND: C601.2, C602.2, C603.2, C604.2, C605.2, C606.2, C607.2, C608.2, IC601.8 (GND), IC602.8 (GND), IC603.2 (GND), IC604.2 (GND), IC605.8 (GND), IC606.8 (GND), IC607.2 (GND), IC608.2 (GND); also elsewhere on the board

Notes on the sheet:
Encoder LVDS Driver Top Left
Encoder LVDS Driver Top Right
Encoder LVDS Driver Bottom Right

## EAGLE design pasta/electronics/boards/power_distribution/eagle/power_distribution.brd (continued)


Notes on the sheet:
Cable connectors to the motors
Cable connectors to the encoders
Cable connector to the kicker
Cable connector to ball detection



Board: 4 copper layers, 170.0 x 152.0 mm, 170 parts (99 on the bottom side), 188 nets.

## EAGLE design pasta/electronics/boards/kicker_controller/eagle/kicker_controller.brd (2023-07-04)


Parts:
C101, C102, C103, C104, C105, C106: 100n ±10% 50V X7R; C0603
D101: 150066M153000; WL-SFCX_0606
R101, R103, R105, R106, R107: 1k ±1% 75V 0.1W; R0603
R102: 10k ±1% 75V 0.1W; R0603
R104: 2k2 ±1% 75V 0.1W; R0603
U101: STM32F303CC; LQFP48
U102: SN74AHC1G125DBVR; SOT23-5
Y101: 8 MHz; 830207192009

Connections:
+3V3: C101.1, C102.1, C103.1, C104.1, C105.1, C106.1, D101.4, R103.1, U101.1 (VBAT), U101.9 (VDDA), U101.17 (PA7), U101.18 (PB0), U101.24 (VDD_2), U101.36 (VDD_3), U101.48 (VDD_1), U102.5 (VCC), Y101.P1 (EN), Y101.P4 (VCC); also elsewhere on the board
BOOT0: R101.2, U101.44 (BOOT0)
ENABLE_CHARGE_STM: U101.31 (PA10); also elsewhere on the board
ENABLE_DISCHARGE_STM: U101.32 (PA11); also elsewhere on the board
GND: C101.2, C102.2, C103.2, C104.2, C105.2, C106.2, R101.1, R104.1, U101.8 (VSSA), U101.19 (PB1), U101.23 (VSS_2), U101.35 (VSS_3), U101.47 (VSS_1), U102.3 (GND), Y101.P2 (GND); also elsewhere on the board
HEARTBEAT_BLUE: R107.2, U101.45 (PB8)
HEARTBEAT_GREEN: R106.2, U101.43 (PB7)
HEARTBEAT_RED: R105.2, U101.42 (PB6)
IR_FEEDBACK_CON: R102.2; also elsewhere on the board
IR_FEEDBACK_STM: R102.1, R104.2, U101.41 (PB5)
JTCK: U101.37 (PA14); also elsewhere on the board
JTDI: U101.38 (PA15); also elsewhere on the board
JTDO: U101.39 (PB3); also elsewhere on the board
JTMS: U101.34 (PA13); also elsewhere on the board
JTRST: U101.40 (PB4)
KICK_CHIP_STM: U101.30 (PA9); also elsewhere on the board
KICK_LINEAR_STM: U101.29 (PA8); also elsewhere on the board
MISO: U101.27 (PB14); also elsewhere on the board
MOSI: U101.28 (PB15); also elsewhere on the board
unnamed: D101.1 (R), R105.1
unnamed: D101.2 (G), R106.1
unnamed: D101.3 (B), R107.1
NCS: U101.25 (PB12); also elsewhere on the board
NRST: U101.7 (NRST), U102.4 (O)
NRST_: R103.2, U102.1 (OE), U102.2 (I); also elsewhere on the board
OSC_IN: U101.5 (PF0), Y101.P3 (OUT)
SCK: U101.26 (PB13); also elsewhere on the board
VOLTAGE_DATA_STM: U101.16 (PA6); also elsewhere on the board
VOLTAGE_SCK_STM: U101.13 (PA3); also elsewhere on the board

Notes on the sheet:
Light Beam Feedback Voltage Divider
Oscillator
True Color Heartbeat
Reset Separation
MCU
Capacitors for MCU
Capacitors for VDDA
Boot Wiring
Task
Pins
Configuration
SDADC Clock
SDADC Data
Hardware Revision
Mainbus
MSB to LSB: PB1, PB0, PA7
PB12, PB13, PB14, PB15
PA6
PA3
TIM15, 10MHz, 50%
ADC2, 0.1 kSps
GPI, floating
SPI2, fastest, push-pull
Light Beam
PB5
GPI, floating, INT5
Heartbeat
PB6, PB7, PB8
JTAG
PA13, PA14, PA15, PB3
JTAG (s. RM0316, 33.4.13)
Kicker Control
PA8, PA9, PA10, PA11
GPO, fastest, push-pull
TIM4
ChibiOS SysClock
TIM2


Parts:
C201: 100u ±20% 35V; 865080545012
C202: 10u ±20% 6V3 X5R; C0603
C203, C204, C205, C206: 100n ±10% 50V X7R; C0603
C207: 47n ±10% 50V X7R; C0603
F201: 5A; 157T
J201: 61302221121
J202: 61301821121
L201: 742792692; WE-CBF_0603(W=2.6)
L202: WE-GFH_4532_7447669212; WE-GFH_4532
Q201: BSS123; SOT23
R201: 56R ±1% 75V 0.1W; R0603
R202: 100R ±1% 75V 0.1W; R0603
U201, U202: SN74LVC2G34; SOT
U203: FIN1002; SOT23-5
U204: FIN1001; SOT23-5
Z201, Z202, Z203, Z204: ESD8704; UDFN10

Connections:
+3V3: C202.1, C203.1, C204.1, C205.1, C206.1, L201.2, U201.5 (VCC), U202.5 (VCC), U203.1 (VCC), U204.1 (VCC); also elsewhere on the board
+3V3_: J201.11, L201.1
+5V: J201.10
+15V: J201.9
ENABLE_CHARGE_CON: J202.10, U202.4 (2OUT), U202.6 (1OUT), Z204.5 (C4), Z204.6 (D4)
ENABLE_CHARGE_STM: U202.1 (1IN), U202.3 (2IN); also elsewhere on the board
ENABLE_DISCHARGE_CON: J202.12, Q201.3 (D), Z203.1 (C1), Z203.10 (D1)
ENABLE_DISCHARGE_STM: Q201.1 (G); also elsewhere on the board
GND: C201.N (-), C202.2, C203.2, C204.2, C205.2, C206.2, C207.2, J201.5, J201.6, J201.7, J201.8, J201.21, J201.22, J202.5, J202.6, J202.7, J202.8, Q201.2 (S), U201.2 (GND), U202.2 (GND), U203.2 (GND), U204.2 (GND), Z201.3 (A), Z201.8 (A), Z202.3 (A), Z202.8 (A), Z203.3 (A), Z203.4 (C3), Z203.7 (D3), Z203.8 (A), Z204.2 (C2), Z204.3 (A), Z204.4 (C3), Z204.7 (D3), Z204.8 (A), Z204.9 (D2); also elsewhere on the board
IR_FEEDBACK_CON: J202.11, Z204.1 (C1), Z204.10 (D1); also elsewhere on the board
JTCK: J201.15, Z201.5 (C4), Z201.6 (D4); also elsewhere on the board
JTDI: J201.14, Z201.4 (C3), Z201.7 (D3); also elsewhere on the board
JTDO: J201.13, Z201.2 (C2), Z201.9 (D2); also elsewhere on the board
JTMS: J201.12, Z201.1 (C1), Z201.10 (D1); also elsewhere on the board
KICK_CHIP_CON: J202.14, U201.6 (1OUT), Z203.5 (C4), Z203.6 (D4)
KICK_CHIP_STM: U201.1 (1IN); also elsewhere on the board
KICK_LINEAR_CON: J202.13, U201.4 (2OUT), Z203.2 (C2), Z203.9 (D2)
KICK_LINEAR_STM: U201.3 (2IN); also elsewhere on the board
MISO: J201.17, Z202.4 (C3), Z202.7 (D3); also elsewhere on the board
MOSI: J201.18, Z202.5 (C4), Z202.6 (D4); also elsewhere on the board
unnamed: R201.1, U203.5 (RO)
unnamed: L202.2, R201.2
NCS: J201.20, Z202.2 (C2), Z202.9 (D2); also elsewhere on the board
NRST_: J201.16; also elsewhere on the board
SCK: J201.19, Z202.1 (C1), Z202.10 (D1); also elsewhere on the board
VCC: C201.P (+), F201.2, J202.1, J202.2, J202.3, J202.4
VCC_: F201.1, J201.1, J201.2, J201.3, J201.4
VOLTAGE_DATA_CON_N: J202.18, R202.1, U203.4 (RIN-)
VOLTAGE_DATA_CON_P: J202.17, R202.2, U203.3 (RIN+)
VOLTAGE_DATA_STM: C207.1, L202.1; also elsewhere on the board
VOLTAGE_SCK_CON_N: J202.15, U204.3 (DOUT-)
VOLTAGE_SCK_CON_P: J202.16, U204.4 (DOUT+)
VOLTAGE_SCK_STM: U204.5 (DI); also elsewhere on the board

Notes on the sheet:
Input Connector
ESD Protection Diodes
Power Fuse
+3V3 Filter
Output Connector
ADC differential data in + Lowpass
Output Buffers



Board: 4 copper layers, 35.0 x 37.4 mm, 40 parts (24 on the bottom side), 41 nets.

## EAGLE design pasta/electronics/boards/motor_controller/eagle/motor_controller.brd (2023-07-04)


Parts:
C101, C105, C107: 100n ±10% 50V X5R; C0402
C102, C106, C108: 1u ±10% 25V X5R; C0402
C103, C104: 4u7 ±20% 6V3 X5R; C0603
F101: 5A; 157T
J101: 61302221121; HDRV22W64P254_2X11_2794X508X854B
J102: 61302021121; MPN 61302021121
L101: 742792692; WE-CBF_0603(W=2.6)
L102: 782632102; WE-CBF_0603(W=2.6)
R101: 2R2 ±1% 50V 62.5mW; R0402
R102: 1k ±1% 50V 62.5mW; R0402
SHORT101: SHORT4.35
SHORT102, SHORT103: SHORT2.4
U101: SN74AHC1G125DBVR; SOT23-5
Z101, Z102, Z103, Z104: ESD8704; UDFN10
Z105: ESD7004; UDFN10

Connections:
+3V3: C101.1, C104.1, L101.2, R102.1, U101.5 (VCC); also elsewhere on the board
+3V3_: C103.1, J101.11, L101.1, SHORT102.P2
+5V: C102.1, J101.10, J102.16 (13), Z105.1 (C1), Z105.10 (D1)
+15V: J101.9
ENCODER_MISO: J102.6 (18), Z103.5 (C4), Z103.6 (D4); also elsewhere on the board
ENCODER_MOSI: J102.8 (17), Z103.1 (C1), Z103.10 (D1); also elsewhere on the board
ENCODER_NCS: J102.5 (3), Z103.4 (C3), Z103.7 (D3); also elsewhere on the board
ENCODER_SCK: J102.7 (4), Z103.2 (C2), Z103.9 (D2); also elsewhere on the board
GND: C101.2, C102.2, C103.2, C104.2, J101.5, J101.6, J101.7, J101.8, J101.21, J101.22, J102.19 (10), SHORT101.P2, SHORT103.P2, U101.3 (GND), Z101.3 (A), Z101.8 (A), Z102.3 (A), Z102.8 (A), Z103.3 (A), Z103.8 (A), Z104.3 (A), Z104.4 (C3), Z104.5 (C4), Z104.6 (D4), Z104.7 (D3), Z104.8 (A), Z105.3 (A), Z105.8 (A); also elsewhere on the board
HALL_A: J102.13 (7), Z105.4 (C3), Z105.7 (D3); also elsewhere on the board
HALL_B: J102.14, Z105.5 (C4), Z105.6 (D4); also elsewhere on the board
HALL_C: J102.15 (8), Z105.2 (C2), Z105.9 (D2); also elsewhere on the board
JTCK: J101.15, Z101.4 (C3), Z101.7 (D3); also elsewhere on the board
JTDI: J101.14, Z101.2 (C2), Z101.9 (D2); also elsewhere on the board
JTDO: J101.13, Z101.1 (C1), Z101.10 (D1); also elsewhere on the board
JTMS: J101.12, Z101.5 (C4), Z101.6 (D4); also elsewhere on the board
MAINBUS_MISO: J101.17, Z102.5 (C4), Z102.6 (D4); also elsewhere on the board
MAINBUS_MOSI: J101.18, Z102.4 (C3), Z102.7 (D3); also elsewhere on the board
MAINBUS_NCS: J101.20, Z102.2 (C2), Z102.9 (D2); also elsewhere on the board
MAINBUS_SCK: J101.19, Z102.1 (C1), Z102.10 (D1); also elsewhere on the board
MOTOR_A: J102.1, J102.2 (20), J102.4 (19); also elsewhere on the board
MOTOR_B: J102.9 (5), J102.10 (16), J102.12 (15); also elsewhere on the board
MOTOR_C: J102.17 (9), J102.18 (12), J102.20 (11); also elsewhere on the board
unnamed: C107.1, L102.1, R101.2
NRST: U101.4 (O); also elsewhere on the board
NRST_: J101.16, R102.2, U101.1 (OE), U101.2 (I)
PGND: SHORT101.P1; also elsewhere on the board
UART_RX: J102.3 (2), Z104.2 (C2), Z104.9 (D2); also elsewhere on the board
UART_TX: J102.11 (6), Z104.1 (C1), Z104.10 (D1); also elsewhere on the board
VCC: F101.2; also elsewhere on the board
VCC_UNFUSED: F101.1, J101.1, J101.2, J101.3, J101.4
VDDSD: C105.1, C106.1, R101.1, SHORT102.P1; also elsewhere on the board
VREFSD+: C108.1, L102.2; also elsewhere on the board
VSSSD: C105.2, C106.2, C107.2, C108.2, SHORT103.P1; also elsewhere on the board

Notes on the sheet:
Power GND Connection
Module Connector / Input Connector
Motor Connector / Output Connector
Power Fuse
ESD Protection Diodes
+5V Buffer
+3V3 Filter
SDADC Filter
Unidirectional Reset Separation

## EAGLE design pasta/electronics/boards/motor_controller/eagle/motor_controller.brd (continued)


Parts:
C201, C202, C204, C205, C206, C208: 100n ±10% 50V X5R; C0402
C203: 4u7 ±20% 6V3 X5R; C0603
C207: 1u ±10% 25V X5R; C0402
D201: 150066M153000; WL-SFCX_0606
R201, R202, R203, R204, R205: 1k ±1% 50V 62.5mW; R0402
U201: STM32F373V8H6
U202: 24CW1280T-I/CS0668; CS0-4
Y201: 8 MHz; 830207192009

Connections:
+3V3: C201.1, C202.1, C203.1, C204.1, C205.1, C206.1, C207.1, C208.1, D201.4, R201.2, U201.VBAT, U201.VDD@1 (VDD), U201.VDD@2 (VDD), U201.VDD@3 (VDD), U201.VDDA, U201.VREF+, U202.P1 (VCC), Y201.P1 (EN), Y201.P4 (VCC); also elsewhere on the board
BOOT0: R202.2, U201.BOOT0
CONTROLLER_ENABLE: U201.PA8; also elsewhere on the board
CONTROLLER_FAULT: U201.PA12; also elsewhere on the board
CONTROLLER_INHA: U201.PC9; also elsewhere on the board
CONTROLLER_INHC: U201.PD15; also elsewhere on the board
CONTROLLER_INLC: U201.PD12; also elsewhere on the board
CONTROLLER_MISO: U201.PC11; also elsewhere on the board
CONTROLLER_MOSI: U201.PC12; also elsewhere on the board
CONTROLLER_NCS: U201.PA9; also elsewhere on the board
CONTROLLER_SCK: U201.PC10; also elsewhere on the board
CURRENT: U201.PB1, U201.PE13; also elsewhere on the board
EEPROM_SCL: U201.PB6, U202.P4 (SCL)
EEPROM_SDA: U201.PB7, U202.P3 (SDA)
ENCODER_MISO: U201.PA6; also elsewhere on the board
ENCODER_MOSI: U201.PA7; also elsewhere on the board
ENCODER_NCS: U201.PA4; also elsewhere on the board
ENCODER_SCK: U201.PA5; also elsewhere on the board
GND: C201.2, C202.2, C203.2, C204.2, C205.2, C206.2, C207.2, C208.2, R202.1, U201.PC13, U201.PE3, U201.PE4, U201.VSS@1 (VSS), U201.VSS@3 (VSS), U201.VSSA, U202.P2 (GND), Y201.P2 (GND); also elsewhere on the board
HALL_A: U201.PD0; also elsewhere on the board
HALL_B: U201.PC7; also elsewhere on the board
HALL_C: U201.PC8; also elsewhere on the board
HEARTBEAT_BLUE: R205.2, U201.PC1
HEARTBEAT_GREEN: R204.2, U201.PC3
HEARTBEAT_RED: R203.2, U201.PC2
JTCK: U201.PA14; also elsewhere on the board
JTDI: U201.PA15; also elsewhere on the board
JTDO: U201.PB3; also elsewhere on the board
JTMS: U201.PA13; also elsewhere on the board
MAINBUS_MISO: R201.1, U201.PD3; also elsewhere on the board
MAINBUS_MOSI: U201.PD4; also elsewhere on the board
MAINBUS_NCS: U201.PD6; also elsewhere on the board
MAINBUS_SCK: U201.PD7; also elsewhere on the board
unnamed: D201.1 (R), R203.1
unnamed: D201.2 (G), R204.1
unnamed: D201.3 (B), R205.1
NRST: U201.NRST; also elsewhere on the board
OSC_IN: U201.PF0, Y201.P3 (OUT)
UART_RX: U201.PA3; also elsewhere on the board
UART_TX: U201.PA2; also elsewhere on the board
VDDSD: U201.VDDSD3, U201.VDDSD12; also elsewhere on the board
VREFSD+: U201.VREFSD+; also elsewhere on the board
VSSSD: U201.PE14, U201.VREFSD-, U201.VSSSD; also elsewhere on the board

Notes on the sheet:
CPU
MAINBUS MISO Pull-up
Boot Wiring
Oscillator
True Color Heartbeat
EEPROM
CPU Decoupling
VDDA / VREF+ Decoupling
VBAT Decoupling
HW ID: (PE3, PE4, PC13) = 0x00


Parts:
C301: 100n ±10% 50V X5R; C0402
C302: 100u ±20% 35V; 865080545012
C303: 10u ±20% 50V X5R; C1206
C304: 100n ±10% 50V X7R; C0603
C305, C306, C308: 1u ±10% 25V X5R; C0402
C307: 47n ±10% 50V X5R; C0402
R301: FC4L32R010FER; FC4L32
R302: 1k ±1% 50V 62.5mW; R0402
SHORT301: SHORT2.4
U301: INA240A3PWR; TSSOP-8
U302: DRV8350FSRTVR; QFN50P500X500X80-33T345

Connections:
+3V3: R302.2; also elsewhere on the board
CONTROLLER_ENABLE: U302.22 (ENABLE); also elsewhere on the board
CONTROLLER_FAULT: U302.17 (FAULT); also elsewhere on the board
CONTROLLER_INHA: U302.23 (INHA); also elsewhere on the board
CONTROLLER_INHC: U302.27 (INHC); also elsewhere on the board
CONTROLLER_INLC: U302.28 (INLC); also elsewhere on the board
CONTROLLER_MISO: R302.1, U302.18 (SDO); also elsewhere on the board
CONTROLLER_MOSI: U302.19 (SDI); also elsewhere on the board
CONTROLLER_NCS: U302.21 (CS); also elsewhere on the board
CONTROLLER_SCK: U302.20 (SCLK); also elsewhere on the board
CPH: C307.1, U302.1 (CPH)
CPL: C307.2, U302.32 (CPL)
CURRENT: U301.8 (OUT); also elsewhere on the board
DVDD: C308.1, U302.29 (DVDD)
GHA: U302.5 (GHA); also elsewhere on the board
GHB: U302.12 (GHB); also elsewhere on the board
GHC: U302.13 (GHC); also elsewhere on the board
GLA: U302.7 (GLA); also elsewhere on the board
GLB: U302.10 (GLB); also elsewhere on the board
GLC: U302.15 (GLC); also elsewhere on the board
GND: C308.2; also elsewhere on the board
HALL_A: U302.24 (INLA); also elsewhere on the board
HALL_B: U302.25 (INHB); also elsewhere on the board
HALL_C: U302.26 (INLB); also elsewhere on the board
MOTOR_A: U302.6 (SHA); also elsewhere on the board
MOTOR_B: U302.11 (SHB); also elsewhere on the board
MOTOR_C: U302.14 (SHC); also elsewhere on the board
unnamed: R301.S1, U301.2 (IN+)
unnamed: R301.S2, U301.3 (IN-)
PGND: C302.N (-), C303.2, C304.2, C306.2, U302.8 (SLA), U302.9 (SLB), U302.16 (SLC), U302.30 (GND), U302.33 (PAD); also elsewhere on the board
VCC: C303.1, C304.1, R301.P2, SHORT301.P1, U302.2 (VM); also elsewhere on the board
VCP: C305.2, U302.4 (VCP)
VDDSD: C301.1, U301.5 (VS), U301.6 (REF2); also elsewhere on the board
VDRAIN: C305.1, SHORT301.P2, U302.3 (VDRAIN)
VGLS: C306.1, U302.31 (VGLS)
VMOTOR: C302.P (+), R301.P1; also elsewhere on the board
VSSSD: C301.2, U301.1 (NC), U301.4 (GND), U301.7 (REF1); also elsewhere on the board

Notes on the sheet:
Motor Controller
Current Sense Amplifier
Motor Controller Configuration
PWM Mode:
IDRIVE:
Deadtime:
Overcurrent:
1x PWM with synchronous rectification
For all gates 100mA for max. 500ns
50ns
Latched fault with 1us deglitch time
VDS-Level:
100mV
PWM Frequency:
32kHz


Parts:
C401, C402, C405, C406, C407, C409: n.c.; C0402
C403, C404, C408: 1u ±10% 50V X5R; C0603
D401, D402, D403, D404, D405, D406: D15V0M1U2LP3
R401, R402, R405, R406, R413, R415: n.c.; R0603
R403, R404, R407, R408, R414, R416: 0R ±1% 50V 62.5mW; R0402
R409, R410, R411, R412, R417, R418: n.c.; R0402
T401, T402, T403: SIZ260DT

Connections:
GHA: R403.2; also elsewhere on the board
GHB: R404.2; also elsewhere on the board
GHC: R414.2; also elsewhere on the board
GLA: R407.2; also elsewhere on the board
GLB: R408.2; also elsewhere on the board
GLC: R416.2; also elsewhere on the board
MOTOR_A: D402.P2 (ANODE), R401.1, R405.2, R410.1, T401.P10 (VSW); also elsewhere on the board
MOTOR_B: D404.P2 (ANODE), R402.1, R406.2, R412.1, T402.P10 (VSW); also elsewhere on the board
MOTOR_C: D406.P2 (ANODE), R413.1, R415.2, R418.1, T403.P10 (VSW); also elsewhere on the board
unnamed: C406.1, R406.1
unnamed: D402.P1 (KATHODE), R403.1, R410.2, T401.P1 (GH)
unnamed: C405.1, R405.1
unnamed: C401.2, R401.2
unnamed: C409.1, R415.1
unnamed: D401.P1 (KATHODE), R407.1, R409.2, T401.P8 (GL)
unnamed: C402.2, R402.2
unnamed: D406.P1 (KATHODE), R414.1, R418.2, T403.P1 (GH)
unnamed: D405.P1 (KATHODE), R416.1, R417.2, T403.P8 (GL)
unnamed: C407.2, R413.2
unnamed: D404.P1 (KATHODE), R404.1, R412.2, T402.P1 (GH)
unnamed: D403.P1 (KATHODE), R408.1, R411.2, T402.P8 (GL)
PGND: C403.2, C404.2, C405.2, C406.2, C408.2, C409.2, D401.P2 (ANODE), D403.P2 (ANODE), D405.P2 (ANODE), R409.1, R411.1, R417.1, T401.P5 (PGND), T401.P6 (PGND), T401.P7 (PGND), T402.P5 (PGND), T402.P6 (PGND), T402.P7 (PGND), T403.P5 (PGND), T403.P6 (PGND), T403.P7 (PGND); also elsewhere on the board
VMOTOR: C401.1, C402.1, C403.1, C404.1, C407.1, C408.1, T401.P2 (VIN), T401.P3 (VIN), T401.P4 (VIN), T401.P9 (VIN), T402.P2 (VIN), T402.P3 (VIN), T402.P4 (VIN), T402.P9 (VIN), T403.P2 (VIN), T403.P3 (VIN), T403.P4 (VIN), T403.P9 (VIN); also elsewhere on the board

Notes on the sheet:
Halfbridge Drivers



Board: 4 copper layers, 35.0 x 41.4 mm, 90 parts (41 on the bottom side), 80 nets.

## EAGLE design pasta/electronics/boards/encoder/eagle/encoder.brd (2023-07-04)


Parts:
C101: 4u7 6V3; C0805
C102, C105: 100n 6V3; C0603
C103: 10u 6V3; C0603
C104: 10n 50V; C0603
D101: PTVS3V3S1UR; SOD123
J101: 690367281076; MPN 690367281076
R101, R102: 10k; R0603
R103, R104, R105, R106: 100R; R0603
R107, R108: 1k; R0603
T101: BSS123; SOT23-3
U101: AS5048A-HTSP
U102: MAX9130EXT+T; 21-0077G_MXM
U103: SN65LVDS050D; SOIC-16

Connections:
+3V3: C101.1, C102.1, C103.1, C104.1, C105.1, D101.C (KATHODE), J101.10 (1), R101.2, U101.11 (VDD5V), U101.12 (VDD3V), U102.1 (VCC), U103.16 (VCC)
DUMMY+: R104.1, U103.10 (2Y)
DUMMY-: R104.2, U103.11 (2Z)
EN_ENCODER: R101.1, T101.3 (D), U103.12 (DE)
GND: C101.2, C102.2, C103.2, C104.2, C105.2, D101.A (ANODE), J101.1 (10), R102.2, R107.1, R108.1, T101.2 (S), U101.5 (GND(TEST1)), U101.13 (GND), U102.2 (GND_2), U102.5 (GND), U103.8 (GND)
MISO: U101.3 (MISO), U103.15 (1D)
MISO+: J101.2 (9), U103.14 (1Y)
MISO-: J101.3 (8), U103.13 (1Z)
MOSI: U101.4 (MOSI), U102.6 (OUT)
MOSI+: J101.5 (6), R103.2, U102.4 (IN+)
MOSI-: J101.4 (7), R103.1, U102.3 (IN-)
unnamed: R102.1, U101.14 (PWM)
unnamed: R108.2, U103.4 (RE)
unnamed: R107.2, U103.9 (2D)
NCS: T101.1 (G), U101.1 (CSN), U103.3 (1R)
NCS+: J101.6 (5), R105.1, U103.2 (1A)
NCS-: J101.7 (4), R105.2, U103.1 (1B)
SCK: U101.2 (CLK), U103.5 (2R)
SCK+: J101.9 (2), R106.1, U103.6 (2A)
SCK-: J101.8 (3), R106.2, U103.7 (2B)

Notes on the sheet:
Alternativer Stecker: 690367181072
Connection to Main Controller
Inverter for CS
Encoder
LVDS Transceiver for MISO, NCS and SCK
LVDS Receiver for MOSI


Board: 2 copper layers, 22.0 x 52.0 mm, 19 parts (0 on the bottom side), 20 nets.

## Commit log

2023-01-29 pasta: kicker: add version 4
    [kicker.brd, kicker.sch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]
2023-02-18 pasta: kicker: fix some bugs in schematics
    - U203 had the wrong MPN (now replaced by a 3V3 LDO)
    - Increased input capacitor of U203 to 10u 50V (previously 330n 250V)
    - Changed title of U203 block in schematics to be more fitting
    - Fixed MPN of optocouplers (value was right, but MPN was wrong)
    [kicker.brd, kicker.sch]
2023-06-26 pasta: add mechanics
    [0603.ipt, 1-copper.ipt, 1-copper_1.ipt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]
2023-07-04 pasta: add remaining electronics
    [encoder.brd, encoder.sch, kicker_controller.brd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]

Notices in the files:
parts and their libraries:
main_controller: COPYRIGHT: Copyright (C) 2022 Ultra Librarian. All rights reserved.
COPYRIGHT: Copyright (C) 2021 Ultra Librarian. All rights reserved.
